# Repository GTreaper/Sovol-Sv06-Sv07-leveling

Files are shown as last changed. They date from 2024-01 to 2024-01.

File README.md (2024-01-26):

*Don't forget to check out my printables.*
https://www.printables.com/@GT_Reaper

*Sv07/Sv07+ BTT smart filament sensor v2.0*
https://www.printables.com/model/672137-btt-sfs-v20-for-sovol-sv07sv07

# Sovol-Sv06-Sv07-leveling.
A guide on how i have achieved great first layers on the Sv06+ and Sv07+. 

# Never try to:
Home the printer without the pei plate, the sensor will not react against the magnet below it needs the steel plate on to function!

All adjustments and calibrations except BED MESH should be done with the printer cold in room temp to eliminate any thermal expansion.

DONT TOUCH THE Z-TILT BETWEEN THESE STEPS. Z TILT ONLY WHEN YOU ARE CERTAIN EVERYTHING IS LEVELED TO THE FRAME AND ALL STEPS ARE DONE.

# Adjustments/checks that should be done before:

V-Wheel adjustment:

Make sure wheels aren't too tight or lose, being able to turn them by hand but the carriage sitting firm with no play.
Clean the V-wheels and rails/extrusions properly.

Z-Axis lead screws:

Make sure to clean and lube the lead screws properly.
Check that the anti backlash nuts aren't to tighten so they can function properly.
Make sure heatblock is straight and tightened firmly as well as a nozzle.

# STEP 1: Measuring!

Start by homing the printer.
When "homing all" is done, without disabling motors!! Measure the distance from the base of the printer to the top part of X carriage. (See picture 1)
Start from the left side and note the measurement. (Make sure you are holding the caliper as straight as possible and measure twice).

Now measure the opposite side the same way on the equal spot, if its lower or higher than left side continues with the next step.
(You want the measurements as equal as possible, 0.01-0.05mm difference is acceptable but the closer the better).

picture 1:
Step1

# Step 2: Adjusting the X carrige!

Turn the lead screw by turning the coupler on the motor. There will be a slight resistance and it will feel like small steps when turning.

This is because the motor is on and not disabled, making it easier to adjust.

Turn it so the right side goes up or down depending on your measurements. When both sides are at the same height, home the printer and measure again.
(You might have to make a small adjustment again after homing that's ok).
The distance between the X carriage and frame/base of the printer should now be equal or as close as possible on both sides.

# Step 3: Ajusting the bed to the X carrige! (This step is Sv07/Sv07+ specific, for Sv06/Sv06+ see bottom of the page)

Go into the bed level menu (screw tilt) and press reference corner. DO NOT PRESS SCREW ADJUST. (see picture 2).
With the nozzle above the reference screw, do the "paper test" and adjust that screw until you are happy with the distance between the bed and nozzle. DO NOT PRESS SCREW ADJUST!

Picture 2: Refrence corner marked with yellow.

screw tilt07

Home the printer (home all).
Move the bed (Y axis) so the reference screw is below the X Carriage and without any pressure on the bed measure from the bed up to the x carriage same way as previous step (note the distance).

Same principles as before applies here, measure the other side (Front right) and adjust bed using the bed screw until equal distance to the X carrige (same rules apply as before).
Do this with all corners/screws and adjust all to the same distance as the reference corner. (see picture 3).

When you are happy with the distance on all corners, do a screw adjust and in small adjustments make all screws 0.
If you wanna be fully certain repeat the meassurement steps one more time to make final adjustments.

Picture 3:
Step3

# Step 4: Probe calibration!
Home the printer.
Now from fluid or mainsail do a PROBE_CALIBRATE by writing PROBE_CALIBRATE to the console and send. (https://www.klipper3d.org/Probe_Calibrate.html).

This will perform an automatic probe, then lift the head, move the nozzle over the location of the probe point, and start the manual probe tool.
Inside fluidd or mainsail, you should now see a window that lets you adjust the nozzle up or down, the same "paper test" applies here..

Personally I use a feeler gauge with thickness 0.100mm for this, but regular paper will work as well. When happy with the distance and a small pressure on the paper/gauge press accept, Klipper will reboot.
Do a PROBE_ACCURACY after PROBE_CALIBRATION is done. (https://www.klipper3d.org/Probe_Calibrate.html#repeatability-check).

# Before continuing!
Check your bed mesh settings, these are located in the printer.cfg. After trying and adjusting a lot, these are the current values I'm using:
(I have excluded mesh min and max as these shouldn't be changed if you haven't changed anything or are an experienced user that knows why you need to change them).

Sv06+mesh06
Sv07+mesh07

7x7 as probe count usually is more than enough, I'm currently using 9x9 as a testing period.

If your bed is severely warped, then bicubic_tension might need to be lower.

Remember: when changing bed mesh settings in config new bed mesh calibration needs to be done! Save your current parameters so you can revert the settings if it doesn't work like you want it to.
Careful when editing the SV07/SV07+ to not delete any grayed out parameter. These are outcommented by sovol and shouldn't be edited.

# Step 5: PID Tuning and heating! (if you pid tuned not long ago skip the pid tuning)
I recommend to do a PID tuning on the bed and extruder (https://www.obico.io/blog/klipper-pid-tuning/).
When PID TUNING is done, turn on the heat bed to the same temperature (the temperature should be equal to your usual printing temp).
Printing PLA I always have a bed at 60c so I will use this as an example.
Heat the bed to 60c and let it heatsoak for some time (10-15min).
When bed has been heat soaked, do a bed mesh and save.

Now your printer should be leveled and have better accuracy when printing.
These measurements can be taken from time to time to make sure it hasn't started to change.

# Step 6: First layer adjustment!
When all previous steps are done, slice a first layer model sized 150x150-220x220 and print. While printing do fine adjustment to Z offset.
I usually adjust with the lowest value available on the screen or in fluidd/mainsail.. Usually 0.005+-! if I don't immediately see that it needs big adjustments.

Sometimes i find a point where i would like to have it just a tiny more up or down but 0.005 +- is to much.
If thats the case you can write in console while printing, change the x in 0.00x to the adjustment distance you want!

(example SET_GCODE_OFFSET Z_ADJUST=+0.0025 MOVE=1, notice the plus in +0.0025! This will offset Z height with 0.0025mm up from the bed).

To offset Z height up 0.0025mm:

SET_GCODE_OFFSET Z_ADJUST=+0.0025 MOVE=1

To offset Z height down 0.0025mm: 

SET_GCODE_OFFSET Z_ADJUST=-0.0025 MOVE=1

Move=1 means it should be adjusted instantly and not wait for next layerchange, this is important to see any diffrence during the first layer calibration.

# Last words!
Now you should be done.
Hope this made any sense and was easy to understand, your first layer should now be more precise and even.

Some slicer settings that can affect the first layer like gaps or ridging.
Extrusion width, I usually set this to around 110-120% of nozzle diameter.
Flow rate, under extrusion can create gaps due to line width not being correct.
Flkow rate, Over extrusion can make lines overlap too much and create ridges.
Infill/wall overlap %, usually have it set between 30-45%.

If you have any question, I will try to answer them as good as possible.

# Step 3 info on Sv06/Sv06+.
Since this printer has a "non adjustable" bed this cant be done the same way! But there is a common and simple mod to get a super flat bed and bed mesh on these.
Silicone mod as its called, find more info about it here: https://sv06.blakadder.com/Upgrades/silicone-mod/
Doing this before anything else will greatly improve the performance of the Sv06/Sv06+.

# Video on my printers putting down first layers!
https://github.com/GTreaper/Sovol-Sv06-Sv07-leveling./assets/99057390/058156c6-f4a0-4eac-a5d2-d20189e29a8e

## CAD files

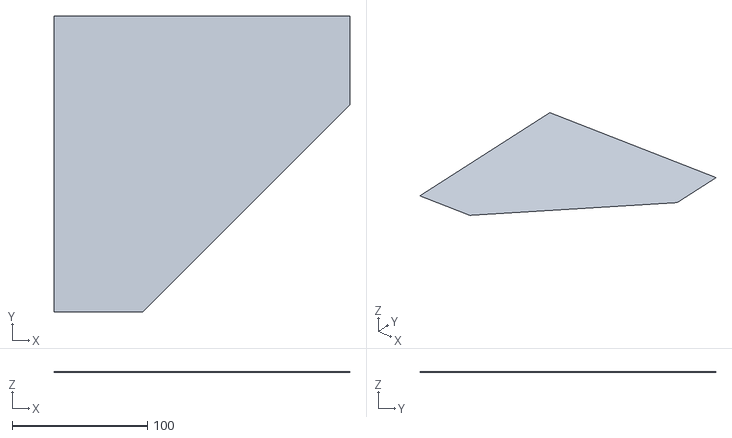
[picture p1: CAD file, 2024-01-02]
First Layer, full 220x220, edge cut.step.stl
219.0 x 219.0 x 0.2

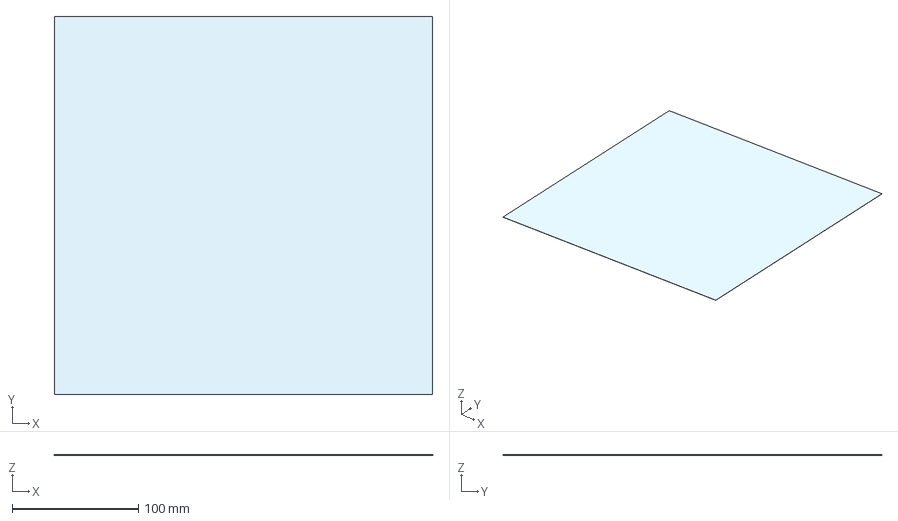
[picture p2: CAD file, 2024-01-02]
First Layer, full 300x300.step
300.0 x 300.0 x 0.2 mm
